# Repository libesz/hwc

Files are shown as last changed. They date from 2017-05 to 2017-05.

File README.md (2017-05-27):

# Hot Water Circulation with AVR

## The problem
This is a tiny project to control a water pump. In a typical domestic hot water system, there is a common problem that the water gets cold in the pipes if some faucets are too far. So you have to waste a lot of water (and time :) ) until you get the hot water, if is was not used recently.

The base of the solution is to build also a returning pipe between the last faucet and the boiler or hot water tank, where a pump can circulate the returning water, so that keeping the pipes hot.

The big question is that based on what event are you going to circulate the water? After a bit of googling you can find these ideas:
* Timer switch, programmed for the typical hot water use times (morning, evening).
* Thermostat: you somehow measure the returning water's temperature and control the pump when needed.
* Detect water usage: there are solutions which can detect when you use any faucet in the house. So you can trigger the circulation by using the e.g. shower for a second, than wait until the hot water arrive before you really start to use it.

## Solution
I was not impressed by any of the solutions above, even not with any combinations. Fortunately I had the pump and the returning pipe built in, so I can control it how I want.
My solution is based on the detection of motion in the house. I have a basic alarm system in the house with passive IR motion sensors in every rooms. The idea is that before every water usage, the people have to walk to the desired faucet. There might be additional time before you need the hot water, like you use the toilet first, for instance :). This time is most probably enough for the pump to get hot water everywhere.
I inspected my alarm system and found a programmable output on the board which can follow any selection of the motion sensors status, so it can trigger this AVR project, which will control the pump for a predefined time.
Also there is a hold timer, which will not switch on the pump ON again if the water is supposed to be still hot in the pipe.

The code is written in C++ and using my base library [from here](https://github.com/libesz/AvrCppBaseLib).

### HW:
* ATTINY45@1MHz
* Opto couplers for both input from the alarm system and towards the output
* 12V relay to control the pump

## Project documentation:
[Link](http://libesz.digitaltrip.hu/automatic-how-water-circulator/)

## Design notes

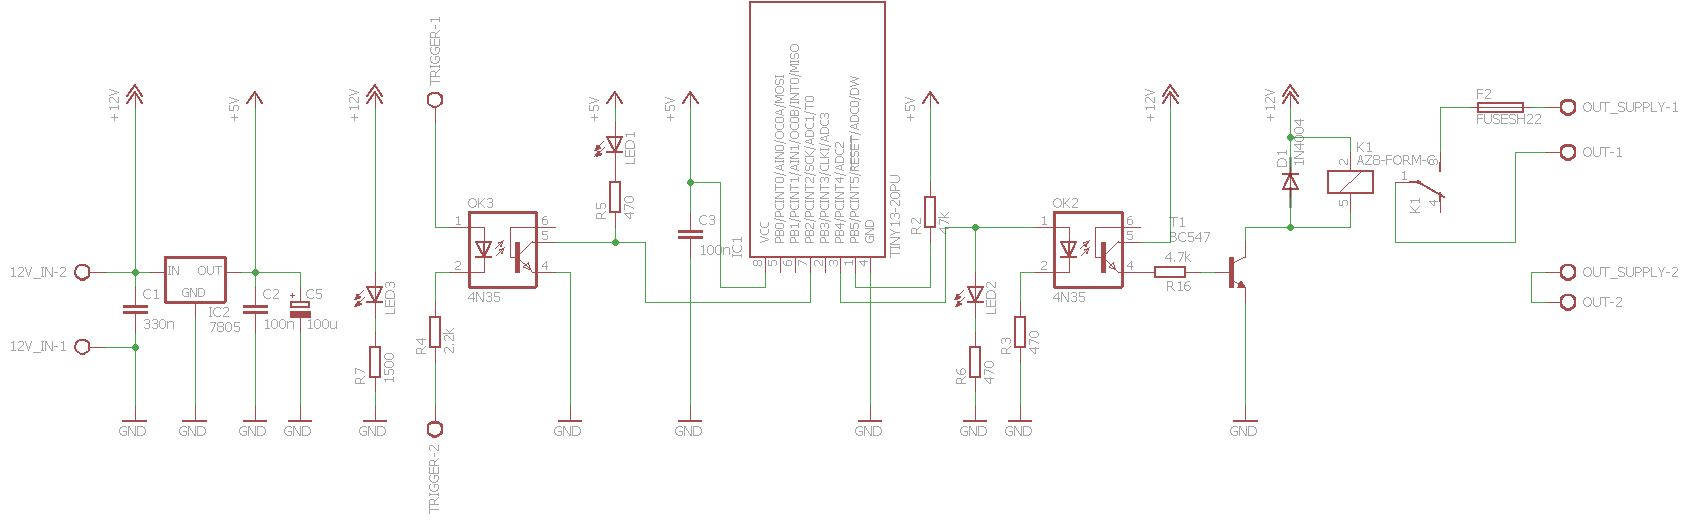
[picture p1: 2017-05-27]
hardware/hwc.png

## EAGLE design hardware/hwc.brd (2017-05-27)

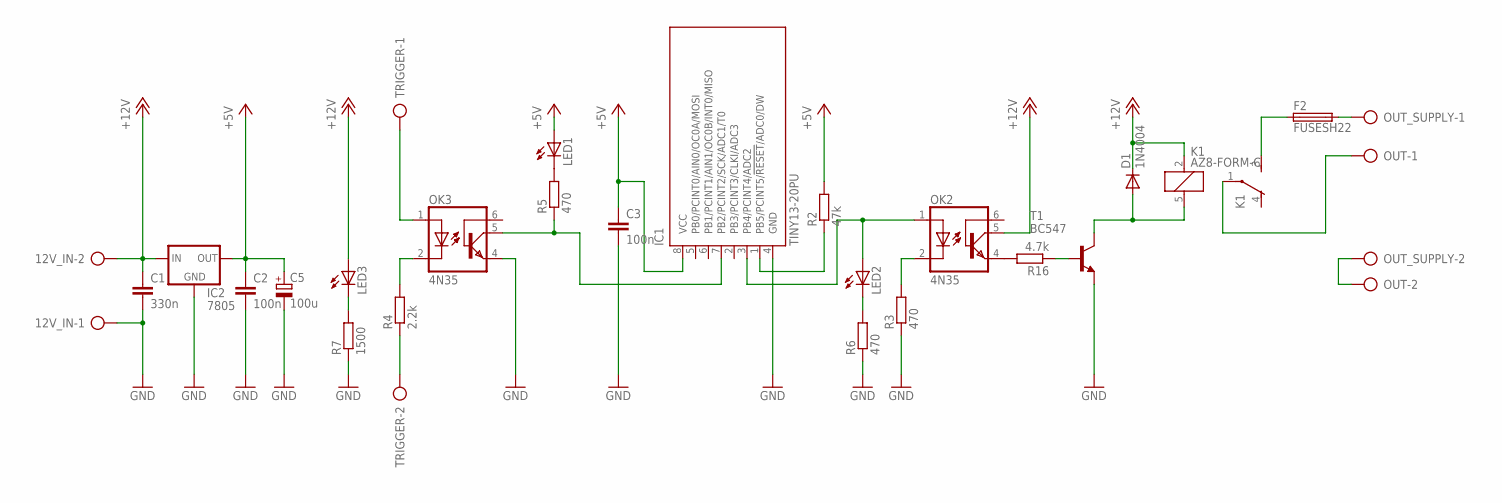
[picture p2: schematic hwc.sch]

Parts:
12V_IN: AK300/2
C1: 330n; C050-025X075
C2, C3: 100n; C050-025X075
C5: 100u; E5-8,5
D1: 1N4004; DO41-10
F2: FUSESH22; SH22
IC1: TINY13-20PU; DIL08
IC2: 7805; 78XXL
K1: AZ8-FORM-C; AZ8
LED1, LED2, LED3: LED5MM
OK2, OK3: 4N35; DIL06
OUT: AK300/2
OUT_SUPPLY: AK300/2
R2: 47k; 0204/7
R3, R5, R6: 470; 0204/7
R4: 2.2k; 0204/7
R7: 1500; 0204/7
R16: 4.7k; 0204/7
T1: BC547; TO92
TRIGGER: AK300/2

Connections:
+5V: C2.1, C3.1, C5.+, IC1.8 (VCC), IC2.OUT, LED1.A, R2.2
+12V: 12V_IN.2, C1.1, D1.C, IC2.IN, K1.2 (1), LED3.A, OK2.5 (COL)
GND: 12V_IN.1, C1.2, C2.2, C3.2, C5.-, IC1.4 (GND), IC2.GND, OK3.4 (EMI), R3.1, R6.1, R7.1, T1.1 (E)
unnamed: IC1.1 (PB5/PCINT5/!RESET!/ADC0/DW), R2.1
unnamed: LED1.K (C), R5.2
unnamed: OUT.2, OUT_SUPPLY.2
unnamed: F2.1, K1.3 (S)
unnamed: K1.1, OUT.1
unnamed: LED2.K (C), R6.2
unnamed: LED3.K (C), R7.2
unnamed: OK2.2 (C), R3.2
unnamed: IC1.3 (PB4/PCINT4/ADC2), LED2.A, OK2.1 (A)
unnamed: F2.2, OUT_SUPPLY.1
unnamed: OK3.2 (C), R4.2
unnamed: OK3.1 (A), TRIGGER.1
unnamed: R4.1, TRIGGER.2
unnamed: IC1.7 (PB2/PCINT2/SCK/ADC1/T0), OK3.5 (COL), R5.1
unnamed: OK2.4 (EMI), R16.2
unnamed: D1.A, K1.5 (2), T1.3 (C)
unnamed: R16.1, T1.2 (B)

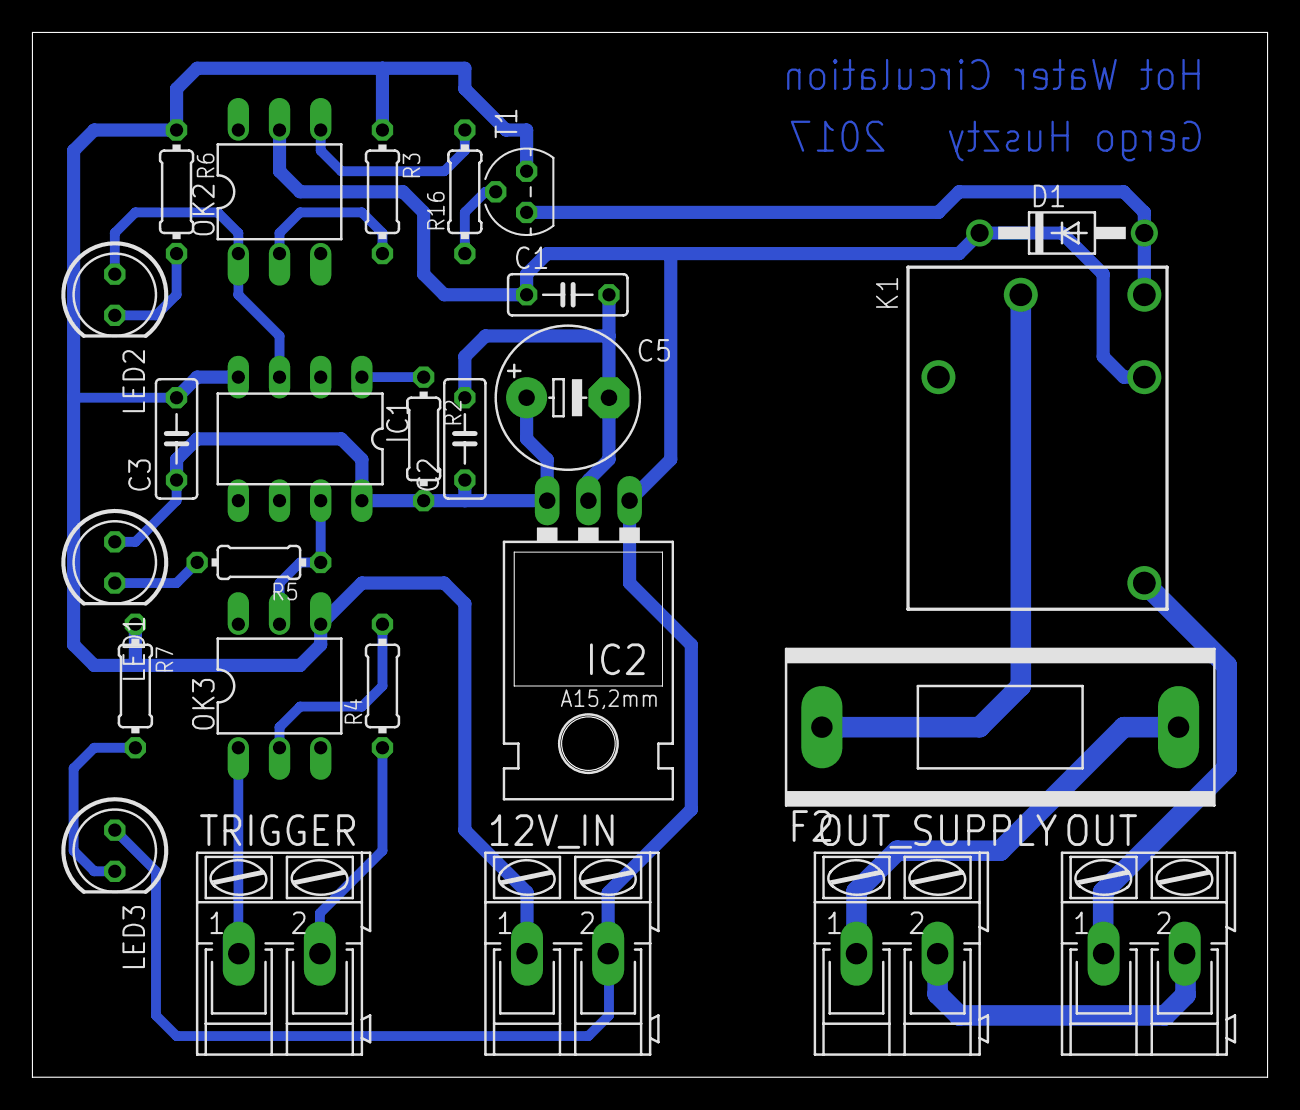
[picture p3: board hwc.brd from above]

Board: 2 copper layers, 76.2 x 64.4 mm, 26 parts (0 on the bottom side), 20 nets.

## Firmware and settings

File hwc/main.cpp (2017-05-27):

/*
 * hwc.cpp
 *
 * Created: 2017.02.08. 20:46:19
 * Author : huszty
 * Chop   : ATTINY45 @ 1MHz
 */ 

#include <avr/io.h>
#include <avr/interrupt.h>

#include "SoftTimerSet.h"
#include "TimedOutput.h"

#include "Trigger.h"

//Config BEGIN
#define OUTPUT_ON_TIME 300
#define TRIGGER_HOLD_OFF_TIME 1500
//Config END

#define OUTPUT_PORT_MASK 1<<4
#define INIT_OUTPUT()  DDRB|=OUTPUT_PORT_MASK;                                 // PORTB3 -> output
#define INIT_TRIGGER() PORTB|=1<<2;MCUCR|=1<<ISC01;GIMSK|=1<<INT0; // PORTB2 -> input (by default), activate pull-up and falling edge interrupt

#define INIT_TIMER0() TCCR0B|=1<<CS02|1<<CS00;TIMSK|=1<<TOIE0; // Set TIMER0 prescaler to 1024; this will cause 3.8 tick/sec (~4HZ)
#define SECOND_PRESCALER 4
volatile unsigned int overflow_counter = 0;

SoftTimerSet<2> gSoftTimerSet;
Trigger *gTrigger = 0;

ISR(TIMER0_OVF_vect) {
  if(++overflow_counter == SECOND_PRESCALER) {
    gSoftTimerSet.tick();
    overflow_counter = 0;
  }
}

ISR(INT0_vect) {
  gTrigger->activate();
}

int main(void) {
  INIT_OUTPUT();
  INIT_TRIGGER();
  INIT_TIMER0();
  TimedOutput output((volatile void *)&PORTB, OUTPUT_PORT_MASK, OUTPUT_ON_TIME);
  gSoftTimerSet.add(&output);
  Trigger trigger(&output, TRIGGER_HOLD_OFF_TIME);
  gSoftTimerSet.add(&trigger);
  gTrigger = &trigger;
  sei();
  while(1);
}

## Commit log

2017-02-26 output is now PORTB2 to have INT0 external interrupt
2017-02-26 facing in timer interrupt
2017-02-26 ON timer changed to 2 minutes.
2017-05-27 timers adjusted (5 mins for output, 25 mins hold-off)
2017-05-27 schematic and board added
    [hwc.brd, hwc.sch]
